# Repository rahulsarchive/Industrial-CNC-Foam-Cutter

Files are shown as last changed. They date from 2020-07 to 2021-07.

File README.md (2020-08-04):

# DIY-CNC-Foamcutter

A DIY Industrial CNC Foam cutter.

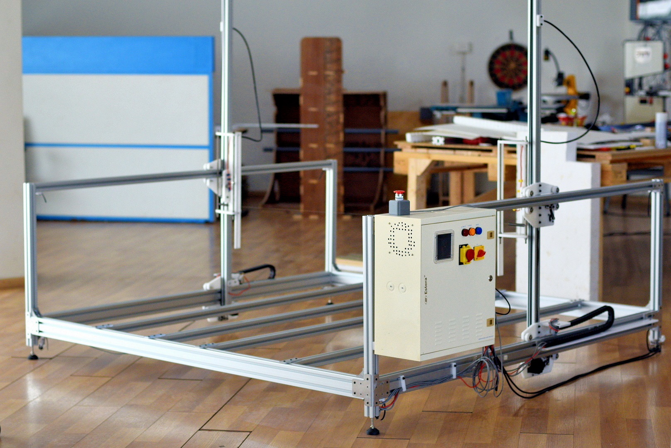
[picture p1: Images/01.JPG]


### Specifications

1. Work Area - 1.6 x 1.6 x 1.5m
2. Power - 220v 6A
3. Heating Element - 26AWG Nichrome wire
4. Heating output - Meanwell DC 52V 700W
5. Max Cutting Feedrate - 2000mm/min
6. Controller - Mach3 USB
7. Stepper Drivers - Rhino Motion Controls
8. Max Paralel lines - 5 Nos

First version using Arduino and Ramps

[4-Axis Foam cutter(Arduiono +Ramps)](https://github.com/rahulsarchive/4AxisFoamCutter)

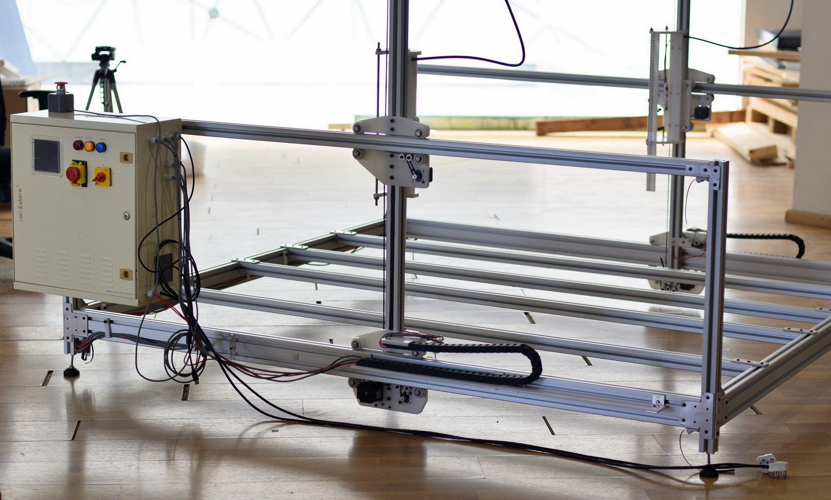
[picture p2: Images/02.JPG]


The frame made from 4040 Extruded Aluminum profiles and joined together with custom Aluminum brackets for rigidity.

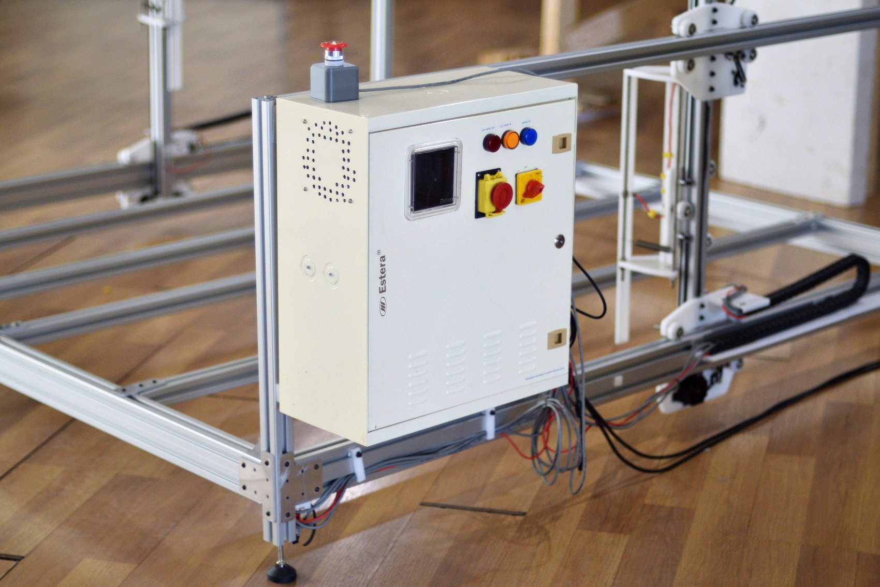
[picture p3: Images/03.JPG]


Control box securely mounted on the side of the machine.

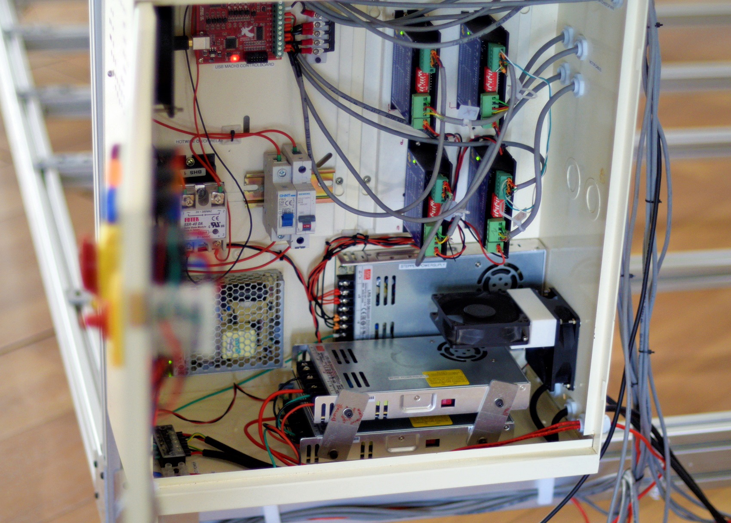
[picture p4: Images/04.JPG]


Original Meanwell powersupplies and Rhino Motion control Drivers.

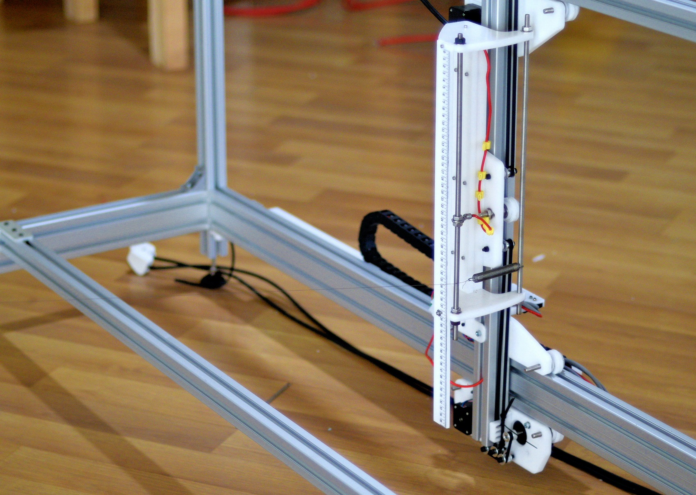
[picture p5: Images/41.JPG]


Y carriage CNC machined from 10mm Delrin.

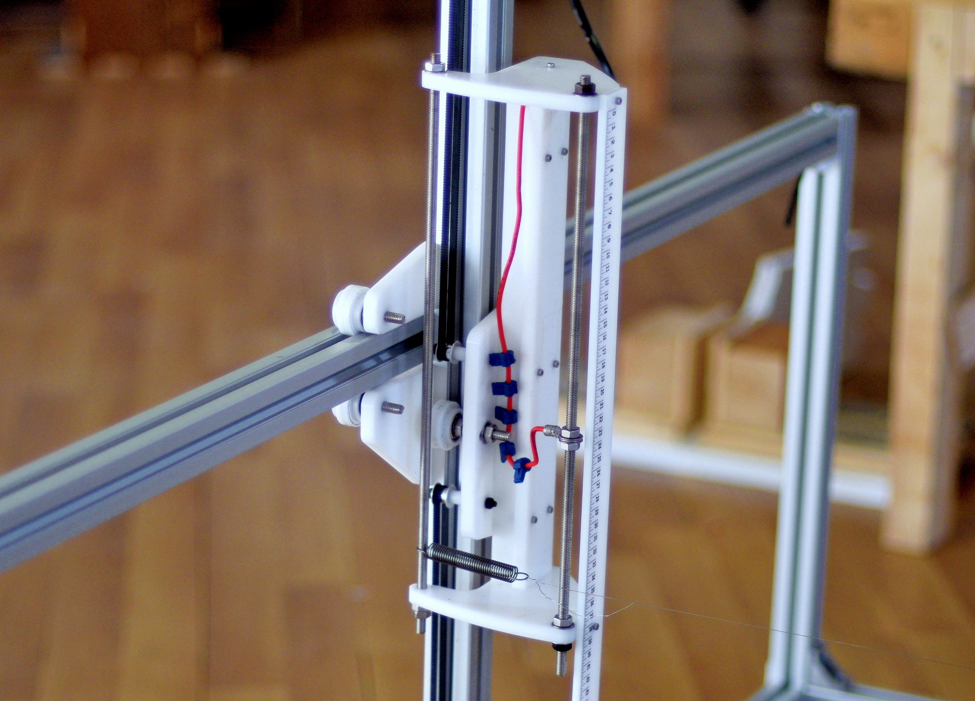
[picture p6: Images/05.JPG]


The nichorome wire is held in the carriage with spring on either side. Power to the wire is fed via the stainless steel threded rods which also act as vertical spacers between parallel wires.

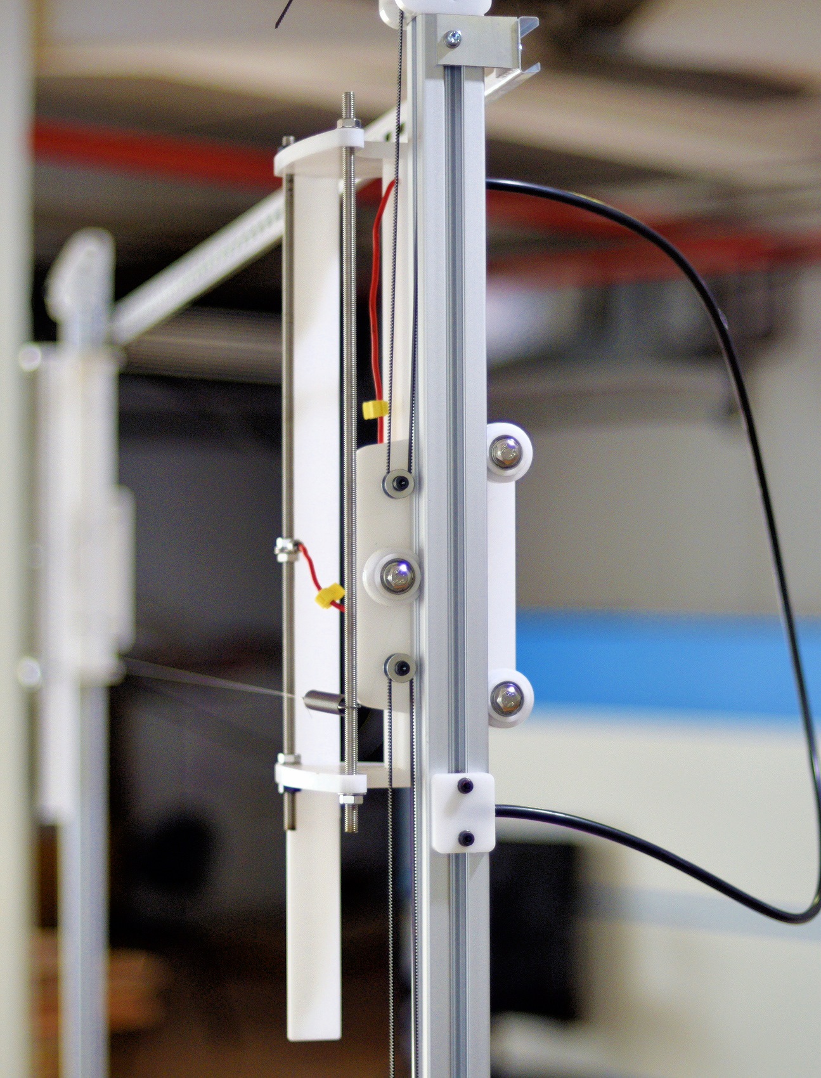
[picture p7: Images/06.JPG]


The carriage runs on roller bearings with custom Delrin bushings which attach to the aluminum profiles. All the wire are contained in the frame itself and the design are modular.

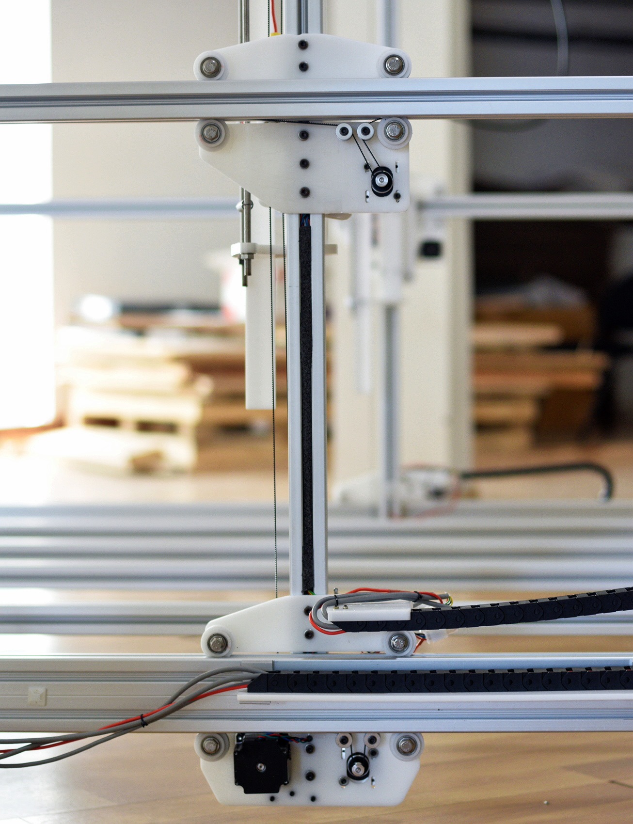
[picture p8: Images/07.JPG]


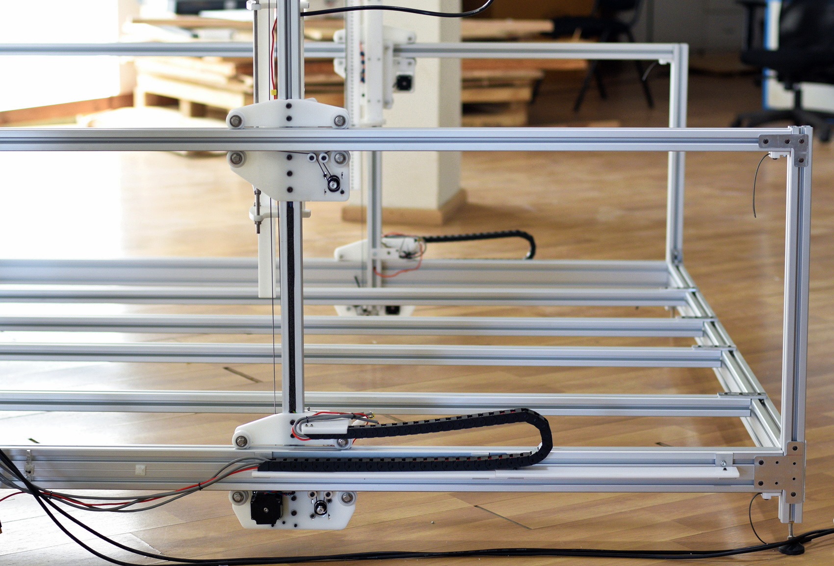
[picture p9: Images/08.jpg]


The x-axis consits of two motors on each side, one on top and bottom to provide longitudinal stability. These are Nema 17 and they run on belts on either side.

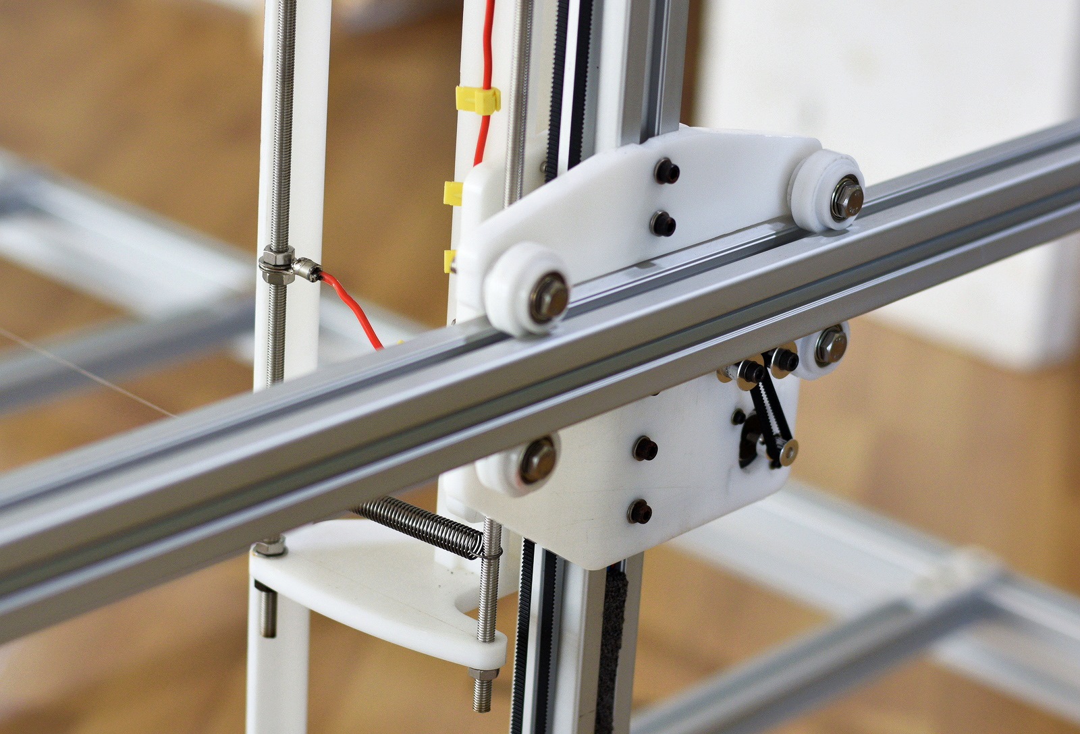
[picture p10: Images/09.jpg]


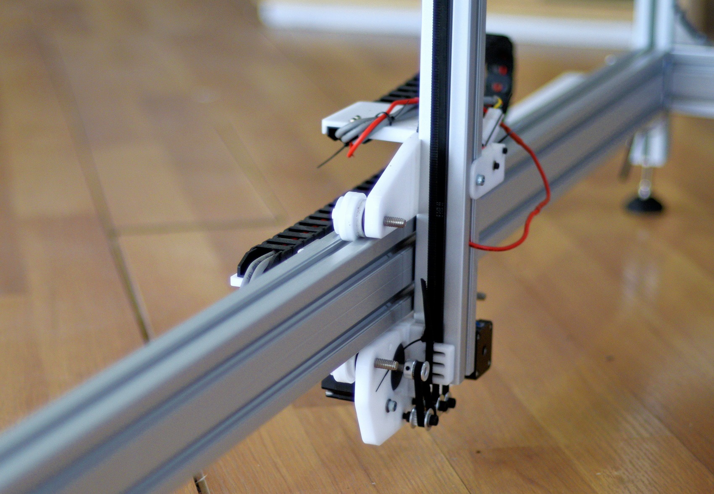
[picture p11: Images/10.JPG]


The Y-axis holds a Nema 23 motor with the belt running through the inner profile of the Aluminum extusions. The wires from the control box are fed via a cable carrier.

The first machine was installed at an insulation profile making factory in Kozhikode. Some photos of the machine in the client's factory.

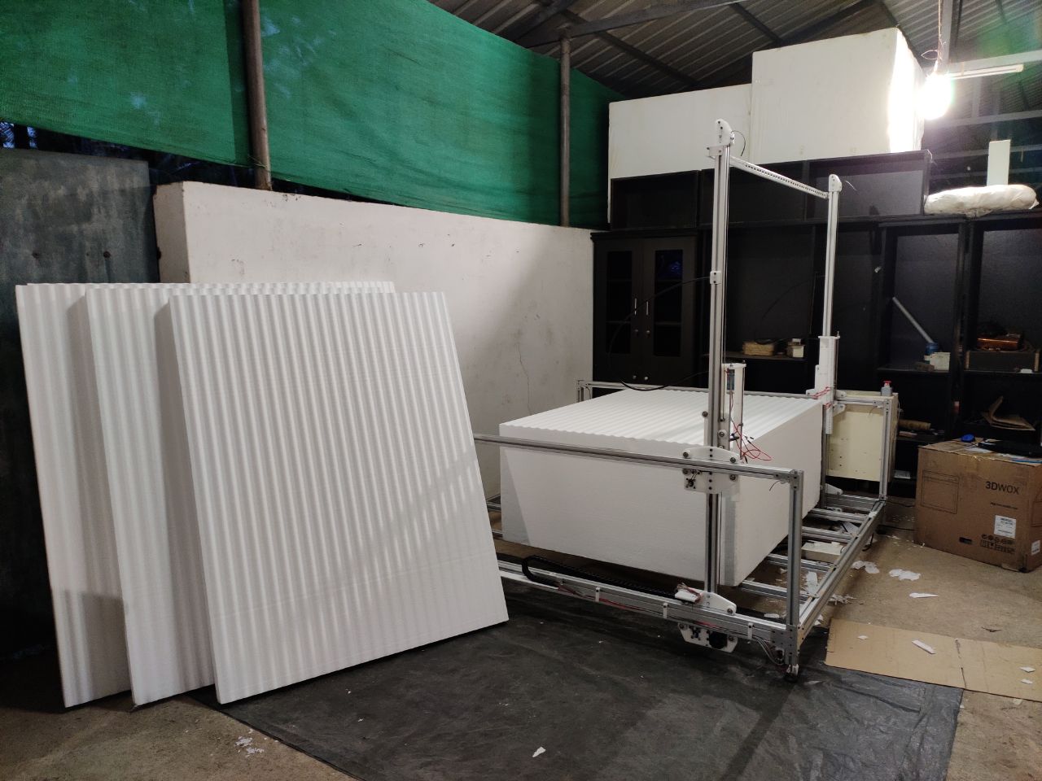
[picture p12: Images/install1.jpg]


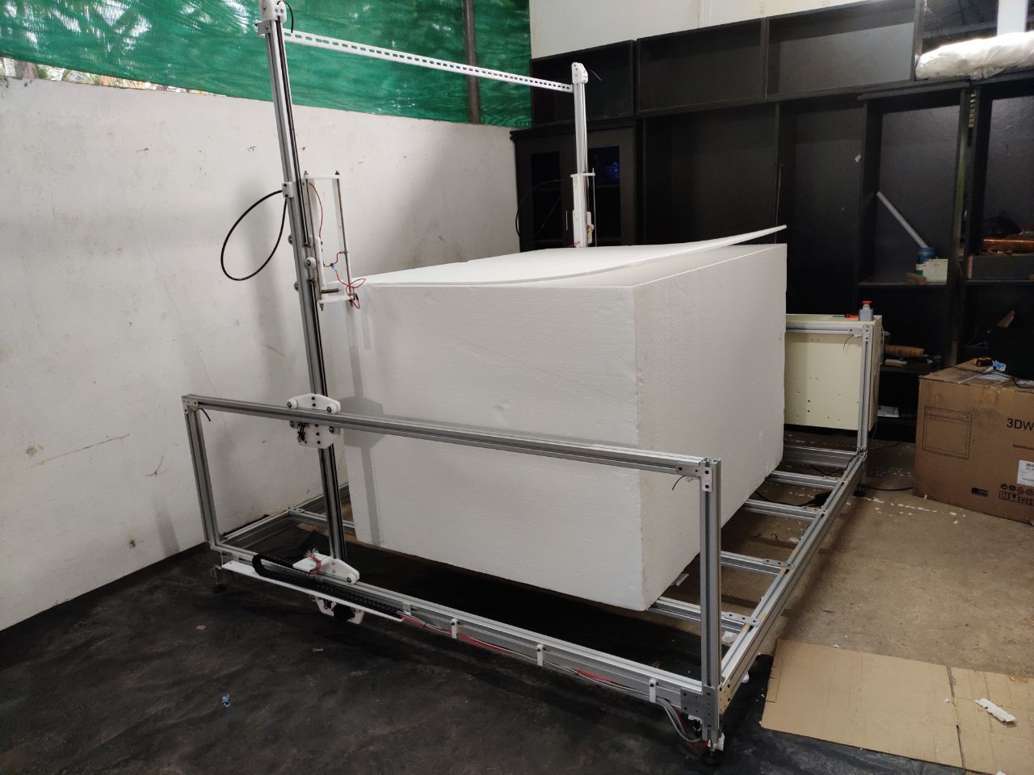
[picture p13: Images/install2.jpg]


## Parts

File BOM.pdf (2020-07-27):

## CNC FOAM CUTTER BOM

Sl no | Item | Qty
1 | 24V 5A Power Supply | 1
2 | 36V 7.5A Power Supply | 1
3 | 24V 15A Power Supply | 2
4 | Mach 3 USB Controller | 1
5 | Rhino Stepper Driver | 4
6 | Nema 23 Stepper motor | 2
7 | Nema 17 Stepper motor | 4
8 | Steel Extension Spring, 25mm x 5mm | 10
9 | Circuit Breaker | 2
10 | 4040 Hammer Nut and Bracket | 120
11 | 4040 T-nut | 140
12 | 2.8mm connector Terminal | 4
13 | Emergency stop switch | 1
14 | Nylon ties | 1 box
15 | Limit switch | 4
16 | Silicon Wire 18 AWG | 20m
17 | M3 Brass Nylon Stand offs | 6
18 | Crimp Terminals Crimping Tool | 1 box
19 | NVR Switch Insulated wire connetors | 1
20 | 4 Core sheilded cable | 25m
21 | Power Cable | 8m
22 | Wire cutter crimping tool | 1
23 | 3 Core Sheilded cable | 20m
24 | Cable tag Zip tie | 1 box
25 | Solid State Relay 40A | 1
26 | 3 Phase Meter box | 1
27 | Cable Gland | 15
28 | Solid state radiator | 1
29 | USB B cable 3m | 1
30 | 220V cooling Fan | 1
31 | Thermal Paste 30g | 1
32 | 100mm Heat sink | 1
33 | 26 Guage Nichrome wire | 20m
34 | M5x12mm Scoket screw | 150
35 | 6mm GT2 timing belt | 20m
36 | 30mm Tension Spring | 10
37 | 4040, 4080 Aluminum Extrusions | 18m
38 | Rotary switch 3 core cable | 1
39 | M5x20 Bolt, M5 Nuts | 50
40 | M5x60 Allen Bolts | 15
41 | M5 20, 25 Allen Bolt | 60
42 | 5/16 bolt, M3x10 Allen Bolt | 20
43 | 2.5mm2 Cable | 20m
44 | SS bolt 5/16 | 30
45 | M8 Hex nut, M8 Threaded rod, Tap Set | 10
46 | 608zz Bearing | 40
47 | M3,M4 screws, Twist drill bits | 1 box
48 | Silicone grease | 1

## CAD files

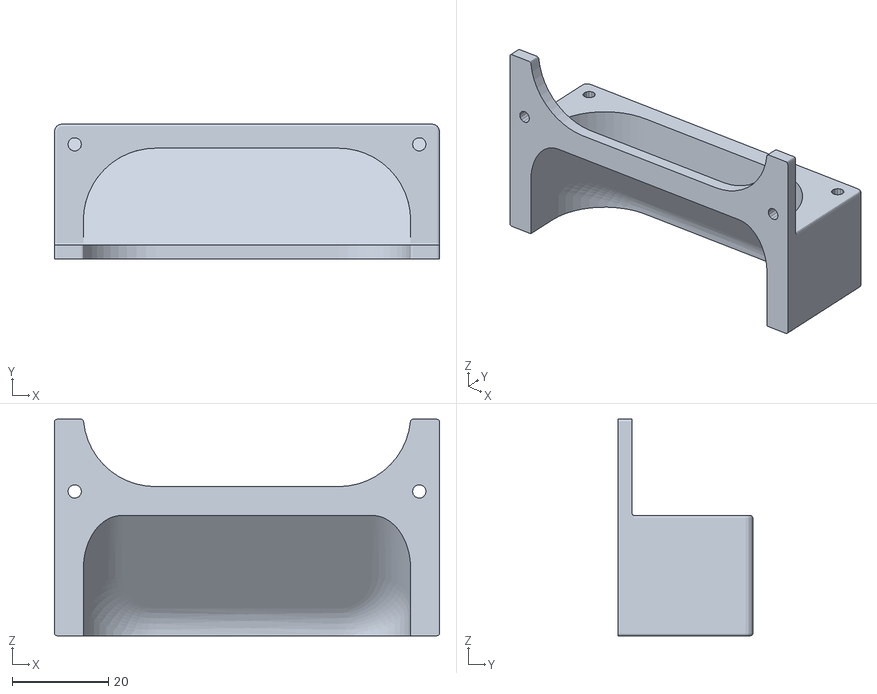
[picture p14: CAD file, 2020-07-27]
Design files/3D print/Fan Holder.stl
80.0 x 28.0 x 45.0

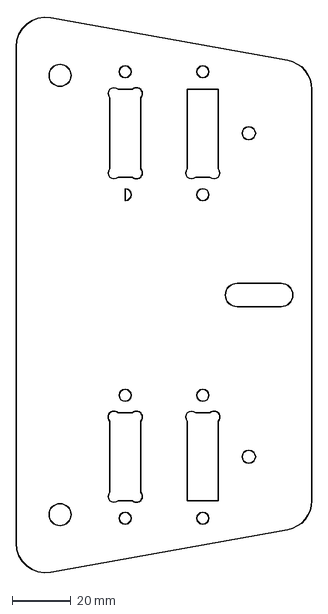
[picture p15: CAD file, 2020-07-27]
Design files/y plate.dxf
101.0 x 190.3 mm

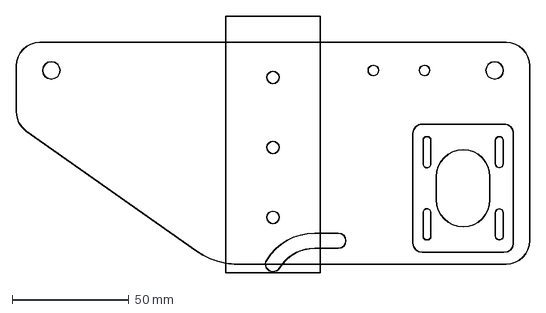
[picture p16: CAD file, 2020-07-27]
Design files/Nema17 motor plate.dxf
220.0 x 110.0 mm

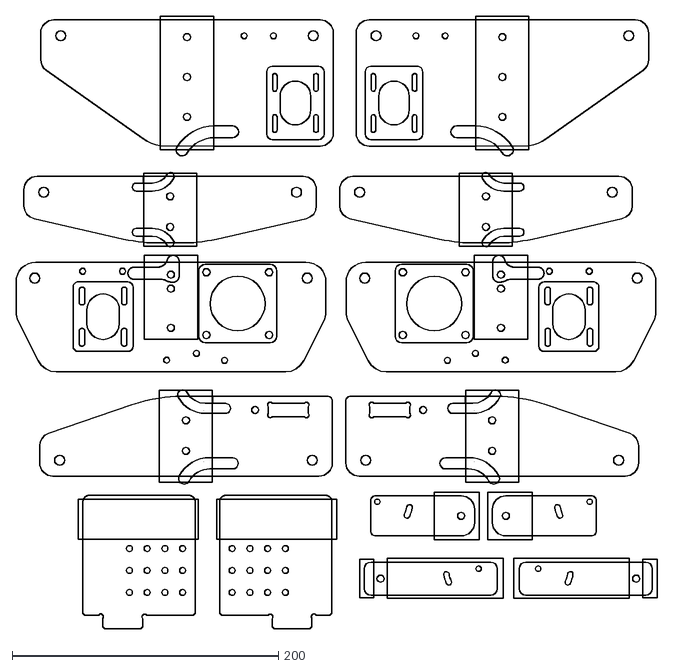
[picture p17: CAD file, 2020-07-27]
Design files/10mm Delrin Mill.dxf
481.9 x 460.8

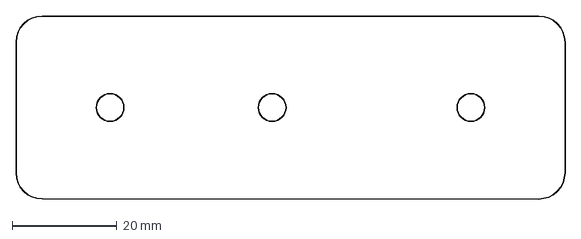
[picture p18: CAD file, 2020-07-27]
Design files/bse brace.dxf
105.0 x 35.0 mm

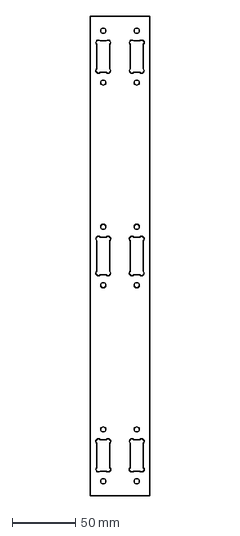
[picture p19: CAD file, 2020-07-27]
Design files/y vert beam support.dxf
47.0 x 379.0 mm

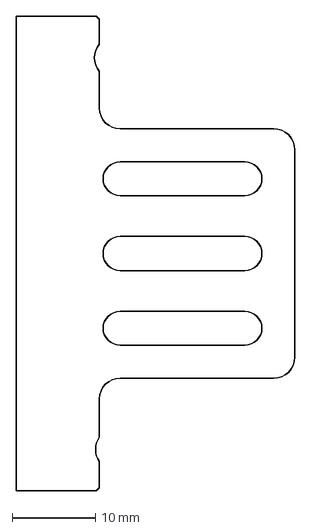
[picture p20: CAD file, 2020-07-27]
Design files/Y cable anchor.dxf
33.5 x 57.1 mm

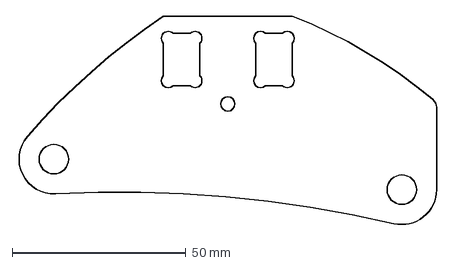
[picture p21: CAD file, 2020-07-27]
Design files/rod insert plate.dxf
120.7 x 60.3 mm

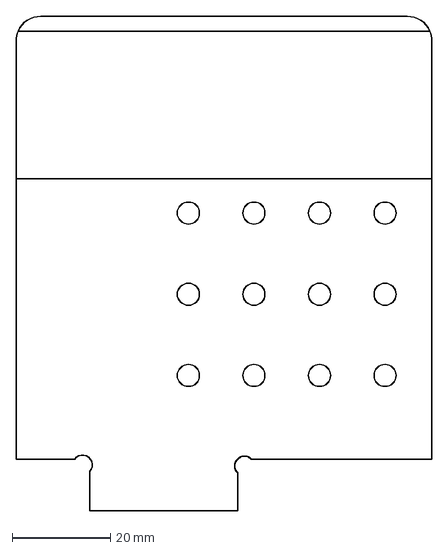
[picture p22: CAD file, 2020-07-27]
Design files/Cablesupport.dxf
84.5 x 100.5 mm

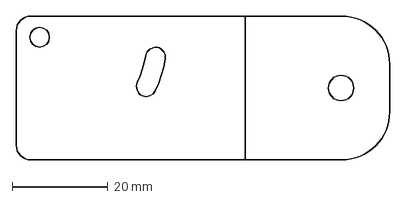
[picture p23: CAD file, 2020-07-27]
Design files/Y limit switch.dxf
78.0 x 30.0 mm

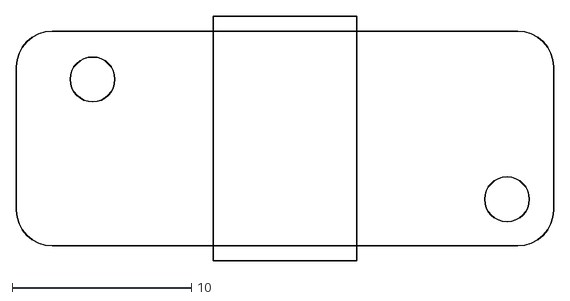
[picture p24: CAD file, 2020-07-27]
Design files/Y anchor belt hold.dxf
30.0 x 13.6

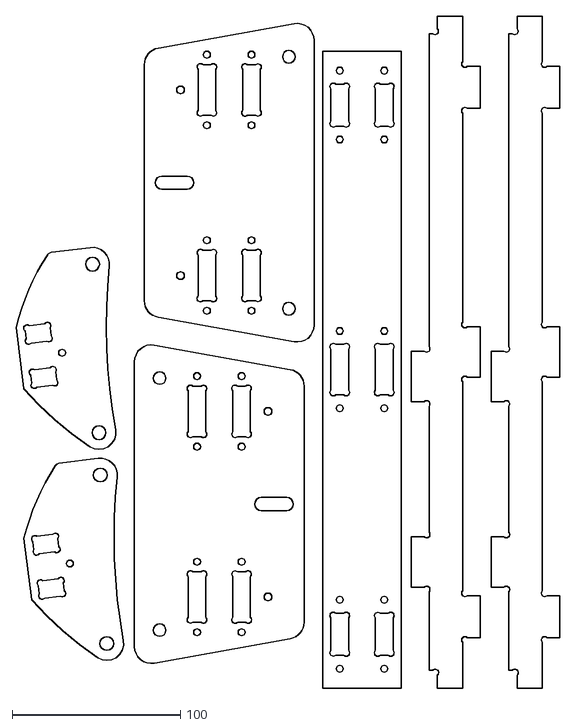
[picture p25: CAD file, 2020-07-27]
Design files/y components.dxf
323.7 x 400.0

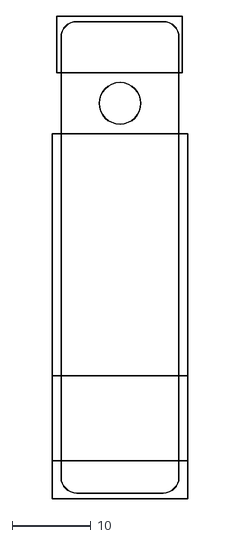
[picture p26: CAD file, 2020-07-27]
Design files/wire organizer.dxf
17.3 x 61.4

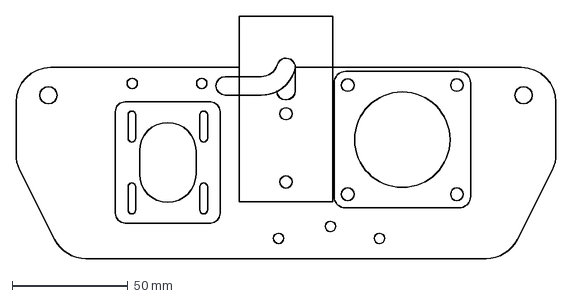
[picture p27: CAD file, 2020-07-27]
Design files/Bottom motr plate.dxf
233.0 x 104.5 mm

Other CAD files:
Design files/Y threaded rod support.dxf
Design files/Y vertical beam.dxf
Design files/Guide roller plate.dxf
Design files/Y mid plate.dxf
Design files/Hot wire delrin parts.3dm
Design files/X limit switch.dxf
Design files/Y Tube holder.dxf
Design files/Y-axis plate.f3d
Design files/y threaded rod support with bearing.dxf

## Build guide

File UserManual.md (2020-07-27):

# User Manual

## Requirements

1. Windows Desktop PC.
2. Mach3 installation file, USB B cable.
3. Utilities and Power.

## Software

#### Mach3

1. Install Mach3 on system (follow Mach3 install guide in Mach folder).
2. Restart the system (mandatory).
3. Copy and paste Hotwire.XML file provided into C:/Mach3/.
4. Connect USB cable to PC, open Mach3, select Hotwire profile.
5. Press reset and Use arrow keys to move the machine, see if the numbers on DRO are changing.

#### Inkscape

1. Go to https://inkscape.org/
2. Download and install inskcape.
3. Go to File>preferences>behaviour decrease the torelance for simplify command.

#### FCNC

1. Go to http://docado.com/FCNC.html
2. Download and install the FCNC software.
3. Open software, load an SVG file, go to settings and set feedrates.

## Workflow 

1. Draw the design in Inkscape.
2. Select the drawing and go to Path settings.
3. Click object to path.
4. Save file as .SVG

5. Open FCNC > load the .svg file.
6. Click show points > right click a point and set start path.
7. Alternateviely, go to Edit> Auto path 
8. Export the design as G-code.

9. Start Mach3, choose the Hotwire profile.
10. Turn on the machine and connect the USB cable.
11. Hit the reset button in the Mach3 panel.
12. Home the machine using the ref all button or if any manual movement, adjust accordinly.
13. Jog the axes using the arrow keys to the start point of the cut.
14. Click zero for all the axes to set the origin point.
15. Click Load G-code button and select the g-code to upload.
16. A preview of g-code will be displayed in the right.
17. Make sure the cutting wire is taught and there is enough material for the design.
18. Click Cycle-Start to start cutting.

## Maintanance

1. Make sure the bearings are tight against the frame.
2. Make sure the belts for all the axes are tight.
3. For tightening the belts of the x-axis,

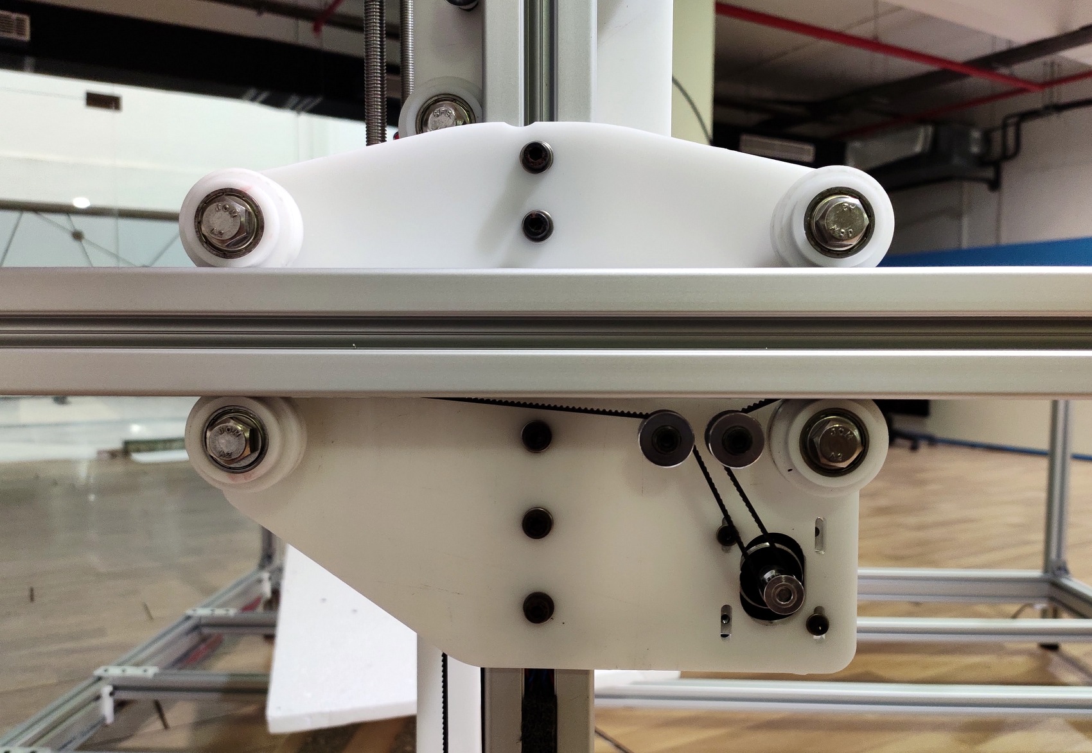
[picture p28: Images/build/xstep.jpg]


	1. loosen the 4 screws in the stepper motor.  
	2. push the motor downwards, and tighten the screws.  
4. For tightening the belts of the y-axis,  

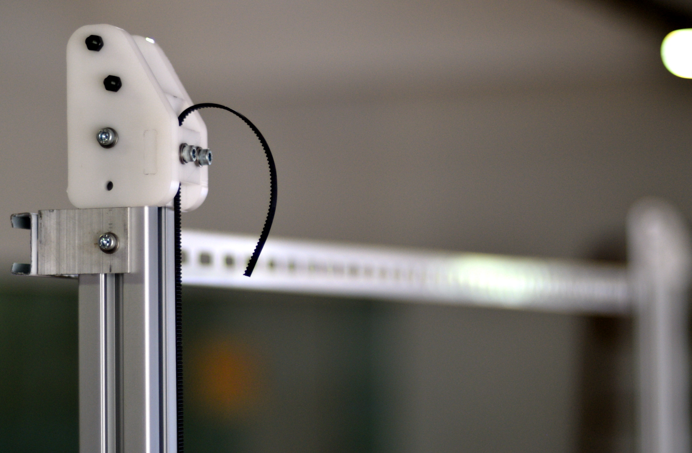
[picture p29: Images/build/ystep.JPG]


	1. loosen the 2 screws at the top of the tower.
	2. pull the bet upwards through the clamping piece.
	3. Move the y-axis back and forth manually.
	4. keep tension on the belt and tighten the 2 screws.
	5. Repeat for the other side.

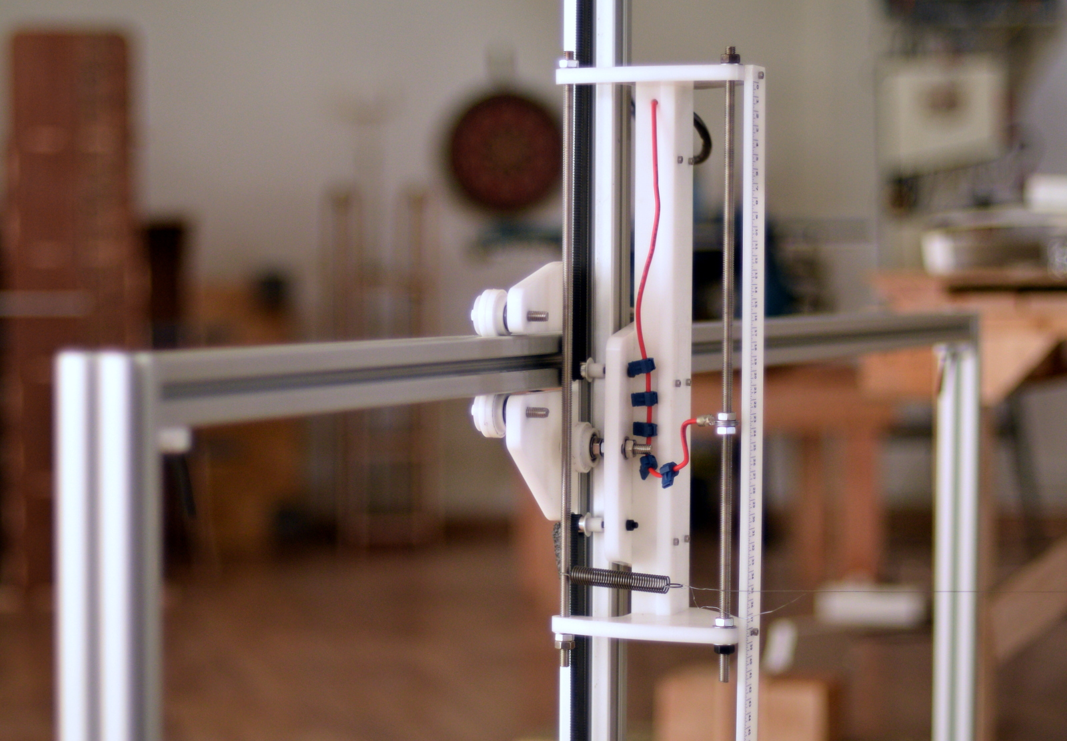
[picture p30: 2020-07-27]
Images/build/DSC_0856.JPG

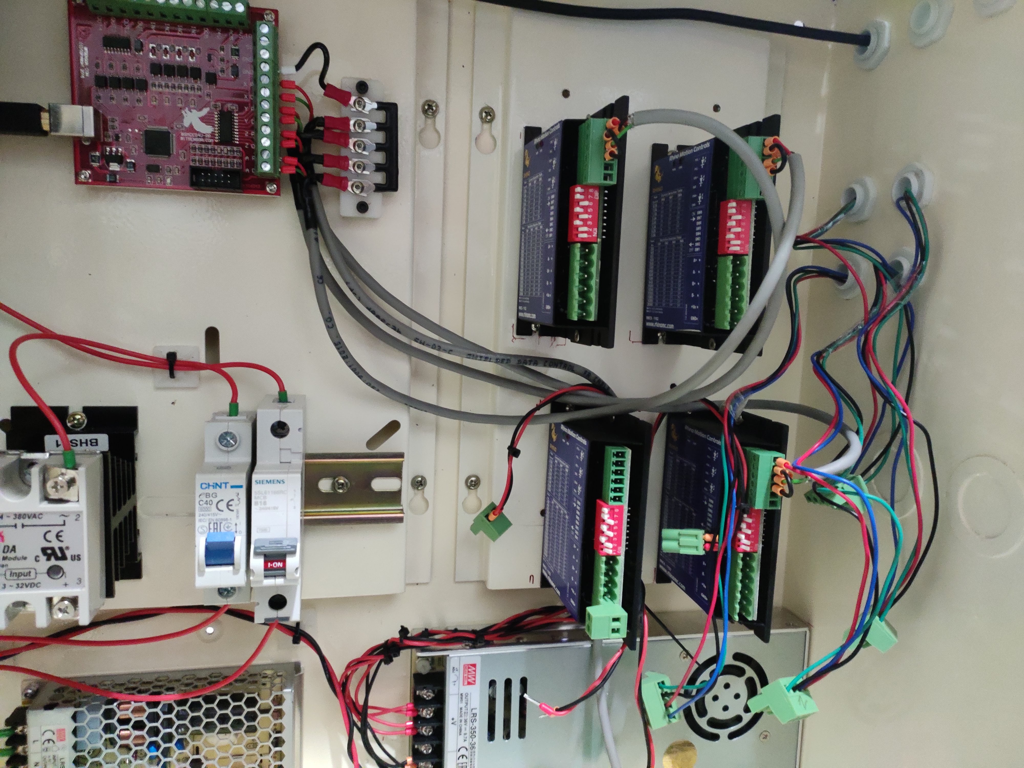
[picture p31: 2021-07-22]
Images/build/6.jpg

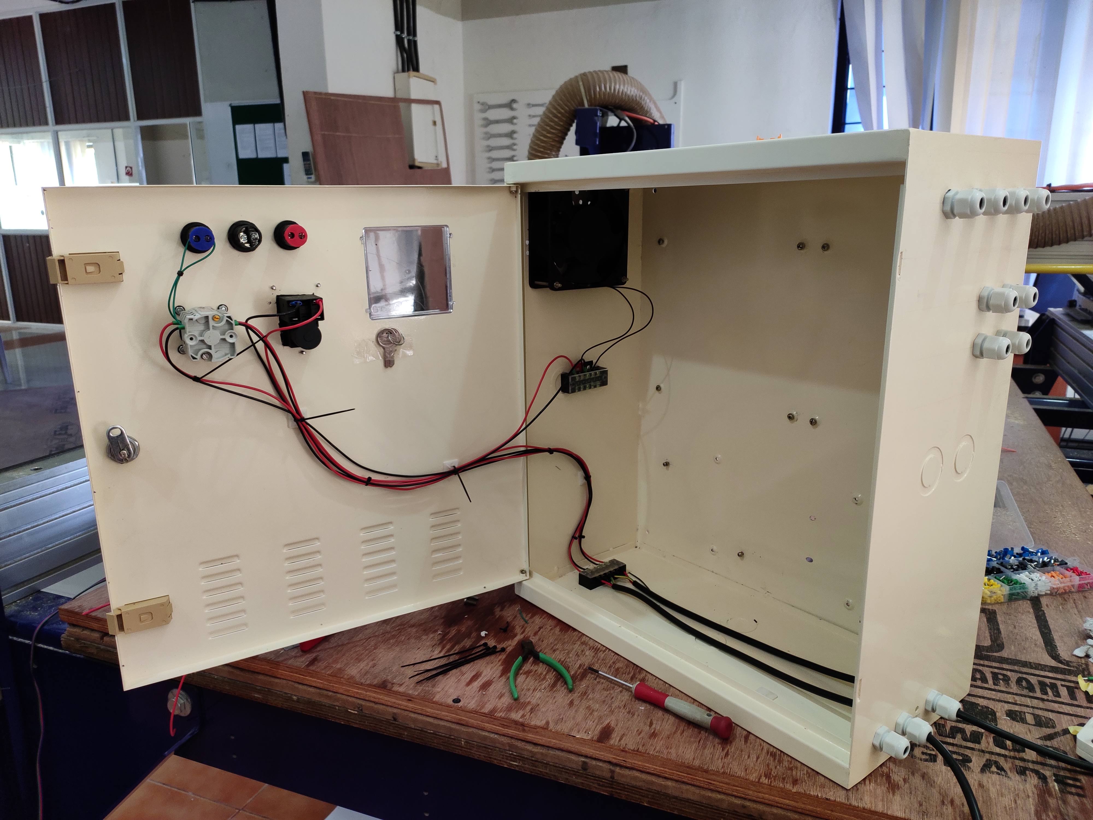
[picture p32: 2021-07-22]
Images/build/2.jpg

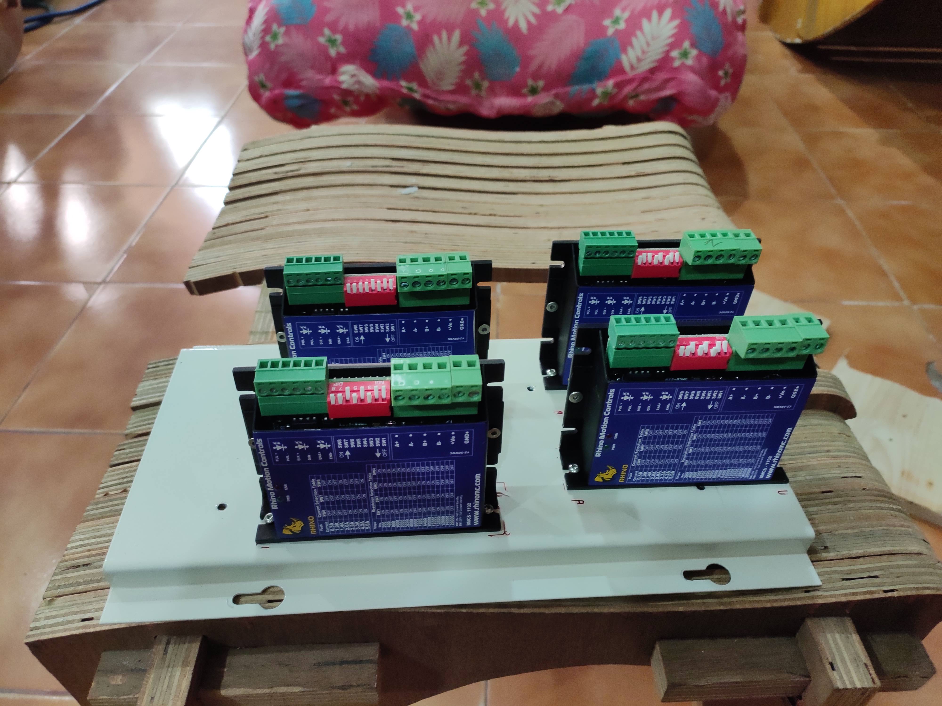
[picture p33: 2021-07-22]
Images/build/4.jpg

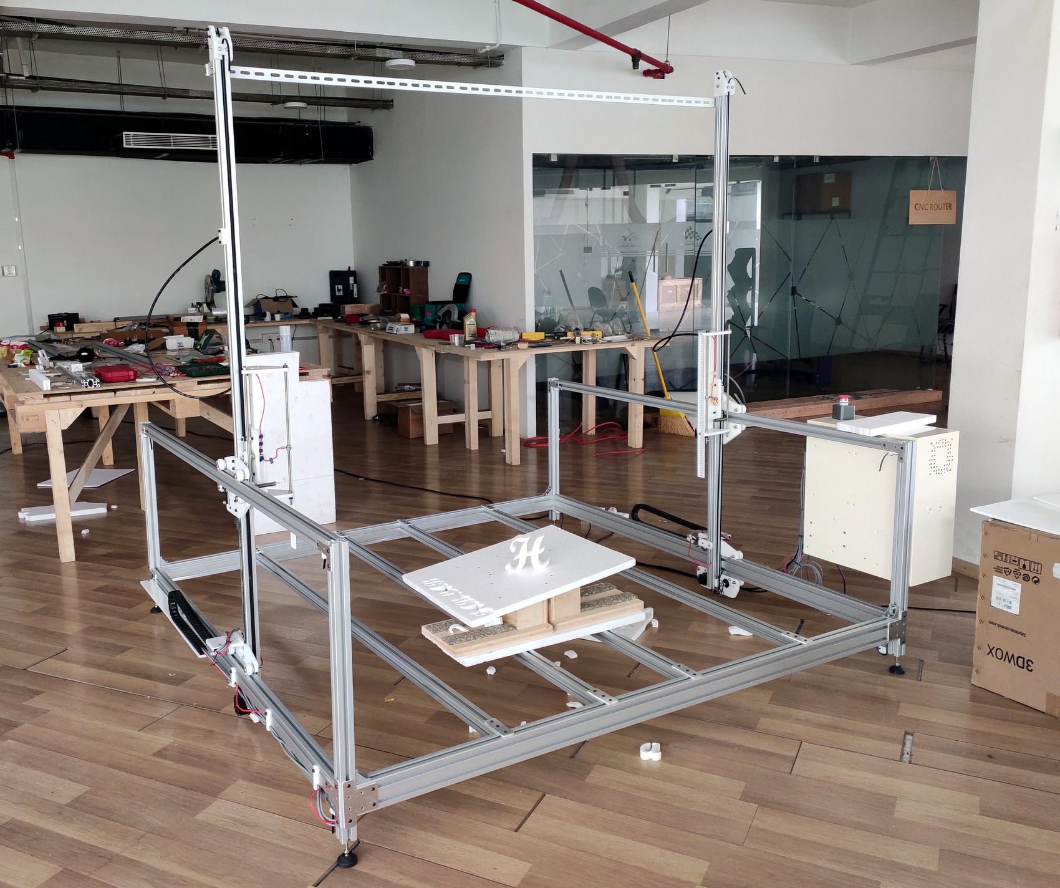
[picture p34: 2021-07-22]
Images/build/IMG_20200723_094812.jpg

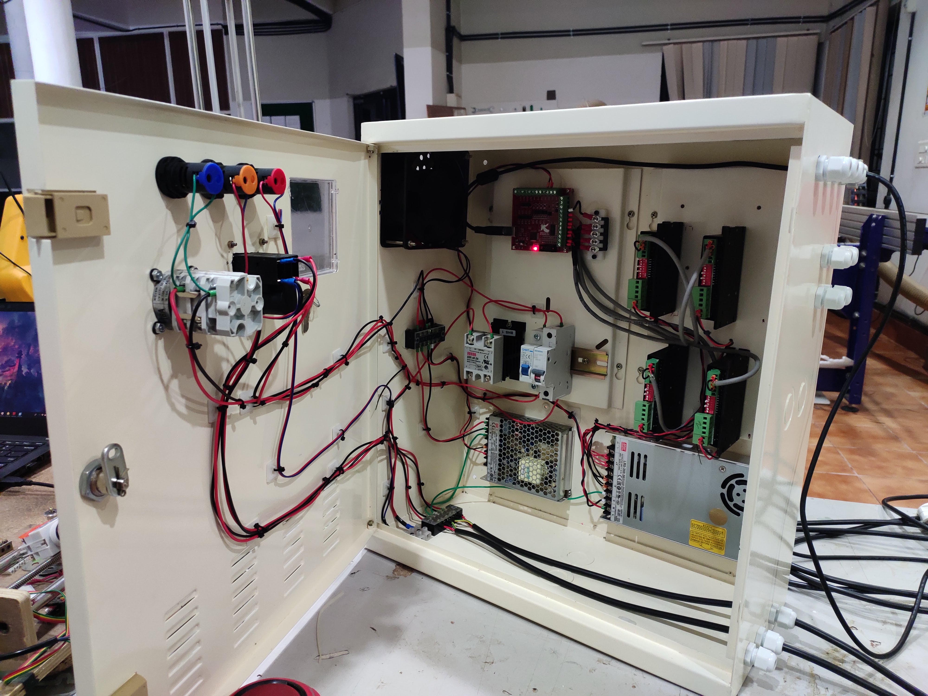
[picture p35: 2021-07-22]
Images/build/7.jpg
